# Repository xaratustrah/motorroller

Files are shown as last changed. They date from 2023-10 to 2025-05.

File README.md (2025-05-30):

# motorroller - Open hardware open software stepper motor controller

<div style="margin-left:auto;margin-right:auto;text-align:center">
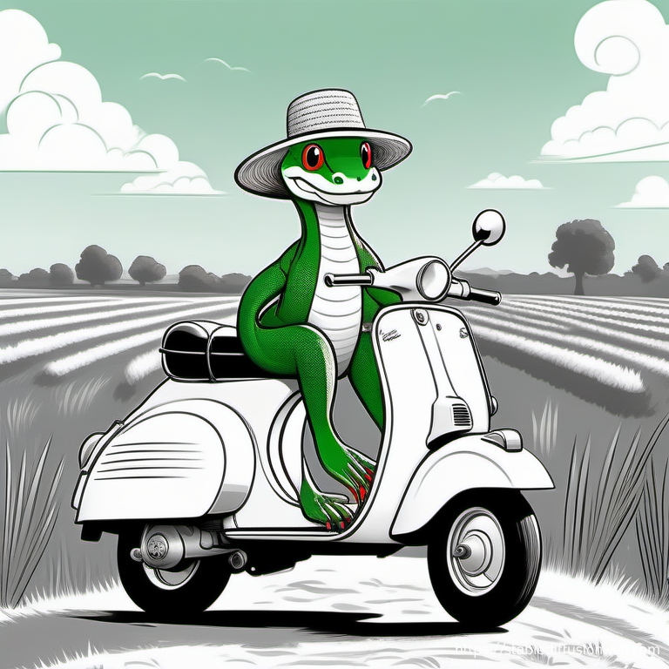
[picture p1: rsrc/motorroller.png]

</div>

`motorroller` is an easy to use open hardware open software stepper motor controller using Raspberry Pi. Depending on which driver you use, you can control 5 phase or 2 phase stepper motors. In this current configuration, it can control up to 4 motors. Also supported are the readout of linear potentiometers.

## Software installation

### Raspberry Pi OS
Please download the latest version of [Raspberry Pi OS Lite](https://www.raspberrypi.com/software/). Newest versions require setting up username / password already in the imager tool. You can also enable SSH from there.

### Raspi-config
Then you can expand file system using the script `raspi-config` and also enable `SPI`.

### Packages
Install some useful packages:

```bash
sudo apt udpate
sudo apt install -y screen mc tree git python3-pip emacs-nox htop sshfs

```

Then install python packages. You may need to provide the command line arg `--break-system-packages`  depending on your system, but be careful with that:

```bash
pip3 install --break-system-packages RPi.GPIO spidev loguru

```

### Repository

Clone and install the repository:

```bash
cd git
git clone https://github.com/xaratustrah/motorroller
cd motorroller
pip3 install --break-system-packages -r requirements.txt
```

The recommended usage is calling the script directly:

```bash
python3 -m motorroller
```

It is also possible to install `motorroller` in the environment, but for this internet connection might be necessary:

```bash
pip3 install --break-system-packages .
```

For uninstalling both you can type:

```bash
pip3 uninstall --break-system-packages motorroller
```

## Usage

### Running modes

`motorroller` can be run in two different modes (the third client/server mode has not been implemented at this stage). It accepts commands in interactive and command line mode. During movement, pressing `ctrl-C` will stop the movement and exit gracefully.

**NOTE:** during any operation, in case of crash due to any reasons, make sure to re-run the code and close down properly, in order to make sure that system is gracefully shut down. This is specially important because of the magnetic break of the motors. The code makes sure that they are gently released after each operation. In case of an unexpected crash it might happen that this gentle close down is not accomplished. So by re-running the code and gently closing again, this will be guaranteed.

#### Interactive mode

this is the default mode. There will be an input prompt for entering commands. Just run:

```bash
python3 -m motorroller
```

The readline history is activated for convenience. You can revisit your older commands by pressing arrow up.

#### Commands as arguments
Use one or several commands directly in the command prompt:

```bash
python3 -m motorroller --command 0i200 0o200
```

Moves motor 0 in and out for 200 steps. Moving motors inside and outside is always in number of steps, but the read out will print out the position values in mm.

### Command structure

Format is XYZ, where X is one of the following:

```
0 --> Motor 0
1 --> Motor 
2 --> Motor 2
3 --> Motor 3

7 --> Both motors 0 and 1
8 --> Both motors 2 and 3

9 --> Read out potentiometers only, the other two positions will be ignored

Y is the direction either I for in or O for out (case insensitive)

Z is the number of steps (int)
```

For example `0i200` means move motor 0 inside 200 steps.

**Special case of command 9:**

Command 9 is just a reader, which means it does not matter what arguments are given, it will always read out the position potentiometers. So in the case of command 9, the only significant value is the number 9 itself, meaning that all other combinations are ignored.

For example the command `9i0` is the same as `9o56879` and so on.

**NOTE:** all commands are case insensitive, i.e. `i`and `I` are equal, same applies to `o`and `O`.

### Other features
Following features work in combination with all above mentioned operation modes:

#### Logger

A logger file name can be provided in order to put actions and readout information together with a time stamp in a log file. You activate the logger by using the `--log` switch:

```bash
python3 -m motorroller --log ./logfile.txt
```

#### Calibration file
Working with a calibration file insures a safer operation. In the calibration file, which is [TOML format](https://toml.io/en/) limits can be set for every motor. You can provide the name of the calibration file as a command line argument:

```bash
python3 -m motorroller --log ./logfile.txt --cal clibration.toml
```

This works for all modes of operation. Here is the structure of the calibration file, with example values:

```toml
# Configuration and calibration file for Motorroller

[general]
minimum_delay = 0.002 # this slows down the movement. recommended value: 0.002

# calibration point format [mm, ADC value]

[mot0]
limit_outside = 30
limit_inside = 70
cal_points = [[90, 869], [10, 3049]]

[mot1]
limit_outside = 30
limit_inside = 70
cal_points = [[90, 857], [10, 3047]]

[mot2]
limit_outside = 30
limit_inside = 70
cal_points = [[90, 831], [10, 3011]]

[mot3]
limit_outside = 30
limit_inside = 70
cal_points = [[90, 877], [10, 3039]]
```

**NOTE:** Calibration point format is [mm, ADC value]. For calibration points, within each pair, please use either floats or integers, TOML format does not allow mixing. As you know the ADC values are always integers, but position values can be floats. If you choose to have a position value that is a float, then you might need to indicate the ADC value also as a float, with ".0" at the end.

For example allowed values: `[90, 831]` or something like `[90.5, 831.0]` but not allowed: `[90.5, 831]`

**NOTE:** Please note that in the current hardware configuration, as motors move inside:

* values in mm increase
* ADC values decrease
* Motor rotation direction would correspond to CCW

## Hardware description

This version of `motorroller` does not use hardware or software PWM, but instead, for increase of accuracy, it uses exact number of steps. This way, you can keep track of the motor motions for more scalability and reproducibility.

#### Board and Schematics

Motorroller

The schematics has been creating using [KiCAD](https://www.kicad.org/). The schematics file is included in the project. A PDF version of the schematics (connection plan) can be found [here](https://github.com/xaratustrah/motorroller/blob/main/rsrc/motorroller.kicad_sch.pdf). Needed parts are listed also in an spread sheet document [here](https://github.com/xaratustrah/motorroller/blob/main/rsrc/motorroller_part_list.ods).

#### Pin configurations

This is the connection table for the 9 pin D-SUB connector:

| Pin # | Signal |
|---|---|
| 1 | End switch outside limit |
| 2 | N. C. |
| 3 | End switch GND |
| 4 | End switch inside limit  |
| 5 | N. C. |
| 6 | Poti GND |
| 7 | Poti runner |
| 8 | Poti PWR |
| 9 | N. C. |

This is the connection table for round motor connector:

| Pin | Signal |
|-----|---|
| A | Blue |
| B | Green |
| C | Red |
| D | Black |
| E | Orange |
| F | N. C. |
| G | N. C. |
| H | N. C. |
| J | N. C. |
| K | N. C. |
| L | Break PWR |
| M | Break GND |

#### Additional hints

* Please note that the driver has direct opto-coupler inputs, whereas the relay board has opto-couplers that are already pulled up to 5V on one side.

* For crimping the wires, please note that for the crimp tool you need to set level 8 for 0.75mm<sup>2</sup> which are the motor cables, and level 5 for 0.14mm<sup>2</sup> cables, which are the end switch and potentiometer cables.

#### End switches

Although end switches are connected in the hardware, please be aware that in the current version the end switches are *NOT* implemented. There is however a "soft" end switch that is implemented, whose ranges are set in the TOML file.

For example: while the full range of motor movements is 0mm to 100 mm, it is possible to set the limits to 30mm to 70mm.

The software based end switch will not allow any further movement when the motor has entered the limit zone. But it still allows moving past the limit when motor enters from an allowed zone.

For example: if the limit is set to 70mm, and the motor is currently at 65mm, then moving the motors by 10mm will move them past the 70mm limit to 75mm. Issuing any further command in that direction will be caught by the software end switch.

For this reason it is important to always move the motors in a series of SMALL movements and always keep an eye on the current position readout on the display.

*IMPORTANT*: please always move motors in smaller number of steps:

For example moving motor 0 inwards for 1000 steps: 0i1000

#### Outlook / future revisions

Here are some suggestions for an upgrade. In case a PCB is created for the project, it is recommended that the following be considered:

* Use SPI based IO-expander **MCP23S08** in order to read the status of the end switches. This one would share the same SCLK, MOSI and MISO lines with the MCP2308 but would need its own chip select signal. This would be then connected to **pin 26** of the Raspberry Pi header.

A hardware platform has been recently developed that can be used for future versions of `motorroller` and can be found [on this repository](https://github.com/DouniaBoudefla/piadcio). Please also have a look at another similar project called [daedalus](https://github.com/xaratustrah/daedalus/).

In order to have the analog signals of the potentiometers and the digital signals of the end switches, one should use the 10-pin header, and connect via flat cable to 9-pin D-SUB connector to the front plate. **Please notice, that the 10-pin connector has a different counting direction if connected to flat-cable D-SUB connectors!**

* Change relay order

For the next revision, the relay order for the BRK signals could be made more symmetric around the relay board connector:

| Pin # | Rev 0 | Rev 0 connection | Future connection |
|---|---|---|---|
| 1 | 5V | 5V | 5V |
| 2 | 5V | 5V | 5V |
| 3 | REL1  | motor_select | motor_select |
| 4 | REL2  | motor_select | motor_select |
| 5 | REL3  | motor_select | motor_select |
| 6 | REL4  | motor_select | motor_select |
| 7 | REL5  | motor_select | motor_select |
| 8 | REL6  | brk0 | brk0 |
| 9 | REL7  | driver_select | brk1 |
| 10 | REL8  | driver_select | driver_select |
| 11 | REL9  | brk1 | driver_select |
| 12 | REL10 | brk2 | brk3 |
| 13 | REL11 | brk3 | brk2 |
| 14 | REL12 | motor_select | motor_select |
| 15 | REL13 | motor_select | motor_select |
| 16 | REL14 | motor_select | motor_select |
| 17 | REL15 | motor_select | motor_select |
| 18 | REL16 | motor_select | motor_select |
| 19 | GND | GND | GND |
| 20 | GND | GND | GND |

* Level shifters
  
This is a nice to have option, just add two level shifters for the CCW and CLW signals. In principle, a level shifter can also replace the darlington array IC ULN2003A , which is a bit of an overkill for the current purpose.

## Licensing

Please see the file [LICENSE.md](./LICENSE.md) for further information about how the content is licensed.

## Acknowledgements

Many thanks to Robert Boywitt, Roland Fischer and Sven Schuhmacher for helping with the connection plans and correct identification of the parts, and Davide Racano for providing help with the mechanical preparation of the enclosure.

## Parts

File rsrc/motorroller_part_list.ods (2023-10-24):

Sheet: Part Numbers
Part list for Motorroller
https://github.com/xaratustrah/motorroller
How many | Part | Brand | Distributor | Distro Order # | Description
2 | - | - | Conrad | 189626 | IC-Fassung Rastermaß: 7.62 mm, 2.54 mm Polzahl (num): 16 Präzisions-Kontakte
1 | AWHW 20G-0202-T | Assmann | RS | 113-5959 | ASSMANN WSW AWHW Leiterplatten-Stiftleiste Stecker Abgewinkelt, 20-polig / 2-reihig, Raster 2.54mm,
4 | AWHW 10G-0202-T | Assmann | RS | 674-1230 | ASSMANN WSW AWHW Leiterplatten-Stiftleiste Stecker Gerade, 10-polig / 2-reihig, Raster 2.54mm, Lötanschluss-Anschluss,
1 | AWHW 40G-0202-T | Assmann | RS | 674-1252 | ASSMANN WSW AWHW Leiterplatten-Stiftleiste Stecker Gerade, 40-polig / 2-reihig, Raster 2.54mm, Lötanschluss-Anschluss
 | AWP 10-7240-T | Assmann | RS | 674-1097 | ASSMANN WSW AWP IDC-Steckverbinder Buchse, gewinkelt, 10-polig / 2-reihig, Raster 2.54mm
2 | AWP 20-7240-T | Assmann | RS | 674-1104 | ASSMANN WSW AWP IDC-Steckverbinder Buchse, gewinkelt, 20-polig / 2-reihig, Raster 2.54mm
2 | AWP 40-7240-T | Assmann | RS | 674-1110 | ASSMANN WSW AWP IDC-Steckverbinder Buchse, gewinkelt, 40-polig / 2-reihig, Raster 2.54mm
4 | DS1033-09FBNSISS-CT | Connfly | Conrad | 1389963 | D-SUB Buchse 180 ° Polzahl (num): 9 Löten
2 | GTR515B | GMT Global | optik-mechanik.de | GTR515B | 5 Phase motor level converter / driver
1 | MCP3208 | Microchip | Conrad | 651465 | Analog to digital converter
1 | Raspberry Pi 3B+ | Raspberry Pi 3B+ | - | - | Raspberry Pi 3B+
1 | - | RS Pro | RS | 188-1318 | RS PRO 19 Zoll Rack Gehäuse 2U Schwarz, 425 mm x 425mm x 84 mm
1 |  | RS Pro | RS | 361-658 | RS PRO Einzeladerleitung 0,75 mm², 18 AWG 100m Blau PVC isoliert Ø 2.7mm 24 / 0,2 mm Litzen
1 |  | RS Pro | RS | 361-709 | RS PRO Einzeladerleitung 0,75 mm², 18 AWG 100m Gelb PVC isoliert Ø 2.7mm 24 / 0,2 mm Litzen
1 |  | RS Pro | RS | 836-0782 | RS PRO Einzeladerleitung 0,75 mm², 18 AWG 100m Grau PVC isoliert Ø 2.7mm 24 / 0,2 mm Litzen
1 |  | RS Pro | RS | 196-4313 | RS PRO Einzeladerleitung 0,75 mm², 18 AWG 100m Grün PVC isoliert Ø 2.7mm 24 / 0,2 mm Litzen
1 |  | RS Pro | RS | 196-4317 | RS PRO Einzeladerleitung 0,75 mm², 18 AWG 100m Rosa PVC isoliert Ø 2.7mm 24 / 0,2 mm Litzen
1 |  | RS Pro | RS | 361-686 | RS PRO Einzeladerleitung 0,75 mm², 18 AWG 100m Rot PVC isoliert Ø 2.7mm 24 / 0,2 mm Litzen
1 |  | RS Pro | RS | 361-642 | RS PRO Einzeladerleitung 0,75 mm², 18 AWG 100m Schwarz PVC isoliert Ø 2.7mm 24 / 0,2 mm Litzen
1 | - | RS Pro | RS | 289-9846 | RS PRO Flachbandkabel , 10-adrig, Raster 1.27mm Nicht abgeschlossen 12,7 mm
1 | - | RS Pro | RS | 289-9896 | RS PRO Flachbandkabel , 20-adrig, Raster 1.27mm Nicht abgeschlossen 25,4 mm
1 | - | RS Pro | RS | 289-9975 | RS PRO Flachbandkabel , 40-adrig, Raster 1.27mm Nicht abgeschlossen 50,8 mm
4 | - | RS Pro | RS | 494-8912 | RS PRO Printklemme / Stecker , THT, 3-polig / 1-reihig, Raster 5mm
2 | - | RS Pro | RS | 897-1332 | RS PRO Printklemme / Stecker, THT, 2-polig / 1-reihig, Raster 3.5mm
4 | - | RS Pro | RS | 137-957 | RS PRO Sub-D Steckverbinder Buchse, 9-polig / Raster 1.27mm, Kabelmontage IDC
1 | 4301.1407 | Schurter | Distrelec | 169-62-956 | Fuse drawer for DD11.0114.1111
1 | DD11.0114.1111 | Schurter | Distrelec | 169-63-555 | Inlet, C14, 250V, Schurter, 1-pole fuse holder, illuminated green
1 | RC320-07 | Schurter | Distrelec | 303-02-323 | Rear cover, protection
5 | SMQ1089 | Signal Construct | Conrad | 185949 | Signal Construct SMQ1089 SMQ1089 LED-Fassung Metall Passend für (LEDs) LED 5 mm Schraubbefestigung
4 | UTG01412SH | SOURIAU-SUNBANK / EATON | Farnell | 2249934 | 12 pol round connector wall mount female
48 | RC16M23K | SOURIAU-SUNBANK / EATON | Farnell | 3652051 | Cup pins for UTG01412SH
1 | ULN2003A | ST | Conrad | 177970 | Darlington array
1 | TPP-65-3512 | Traco Power | Conrad | 1591563 | TracoPower TPP 65-3512 AC/DC-Netzteilbaustein, open frame 24 V/DC 2.71 A
1 | TC-9445344 | TRU Components | Conrad | 2361336 | Relayboard with 16 relays
1 | 1408770 | TRU Components | Conrad | 1408770 | TRU COMPONENTS RJ45-01 RJ45-Einbaubuchse 1408770 Buchse, Einbau, Stecker, gerade Polzahl 8P8C Silber
4 | TC-02747-10-1-00-2 | TRU Components | Conrad | 1560763 | TRU COMPONENTS TC-02747-10-1-00-2 Stiftleiste Rastermaß: 2.54 mm Polzahl Gesamt: 10 Anzahl Reihen: 2
1 | TC-02747-20-1-00-2 | TRU Components | Conrad | 1560662 | TRU COMPONENTS TC-02747-20-1-00-2 Stiftleiste Rastermaß: 2.54 mm Polzahl Gesamt: 20 Anzahl Reihen: 2
1 | TC-02747-40-1-00-2 | TRU Components | Conrad | 1560769 | TRU COMPONENTS TC-02747-40-1-00-2 Stiftleiste Rastermaß: 2.54 mm Polzahl Gesamt: 40 Anzahl Reihen: 2
1 | 1229322 | TRU Components | Conrad | 1229322 | USB-Doppeleinbaubuchse 2.0 Buchse, Einbau USB-06-BK 2 x USB-Buchse Typ A auf 2 x USB-Stecker Typ A mit 60 cm Kabel 12293
1 | L-53 LGD | Kingbright | Conrad | 146030 | Kingbright L 53 LGD LED bedrahtet Grün Rund 5 mm 2 mcd 60 ° 2 mA 2.2 V
1 | L-53 LID | Kingbright | Conrad | 146005 | Kingbright L 53 LID LED bedrahtet Rot Rund 5 mm 5 mcd 60 ° 2 mA 2 V
1 | TC-8990608 | TRU Components | Conrad | 2247652 | TRU COMPONENTS Strom-Kabel Raspberry Pi [1x USB 2.0 Stecker Micro-B - 1x offene Kabelenden] 1.00 m Schwarz
 |  |  |  |  | Schrauben für SUB-D
1 | MH860 | GLENAIR | Farnell | 105992 | GLENAIR MH860 Crimpwerkzeug, Crimpzange, 22-16AWG Contacts
1 | MH86-164G | DANIELS | Farnell | 151779 | Positionierer für Crimpwerkzeuge, Steckverbinder Fci Trim Trio Metalok Bantam Qikmate
1 | RX2025GE1 | SOURIAU-SUNBANK / EATON | Farnell | 105498 | Ausziehwerkzeug, Kontakten der Baureihe TRIM TRIO von Souriau, #16, Souriau Trim Trio

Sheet: Relay Board Connector
Name | Pin # | Function
5V | 1 | PWR
5V | 2 | PWR
REL1 | 3 | BLUE
REL2 | 4 | BLUE
REL3 | 5 | BLUE
REL4 | 6 | BLUE
REL5 | 7 | BLUE
REL6 | 8 | BRK0
REL7 | 9 | DRV-SEL
REL8 | 10 | DRV-SEL
REL9 | 11 | BRK1
REL10 | 12 | BRK2
REL11 | 13 | BRK3
REL12 | 14 | GREEN
REL13 | 15 | GREEN
REL14 | 16 | GREEN
REL15 | 17 | GREEN
REL16 | 18 | GREEN
GND | 19 | PWR
GND | 20 | PWR

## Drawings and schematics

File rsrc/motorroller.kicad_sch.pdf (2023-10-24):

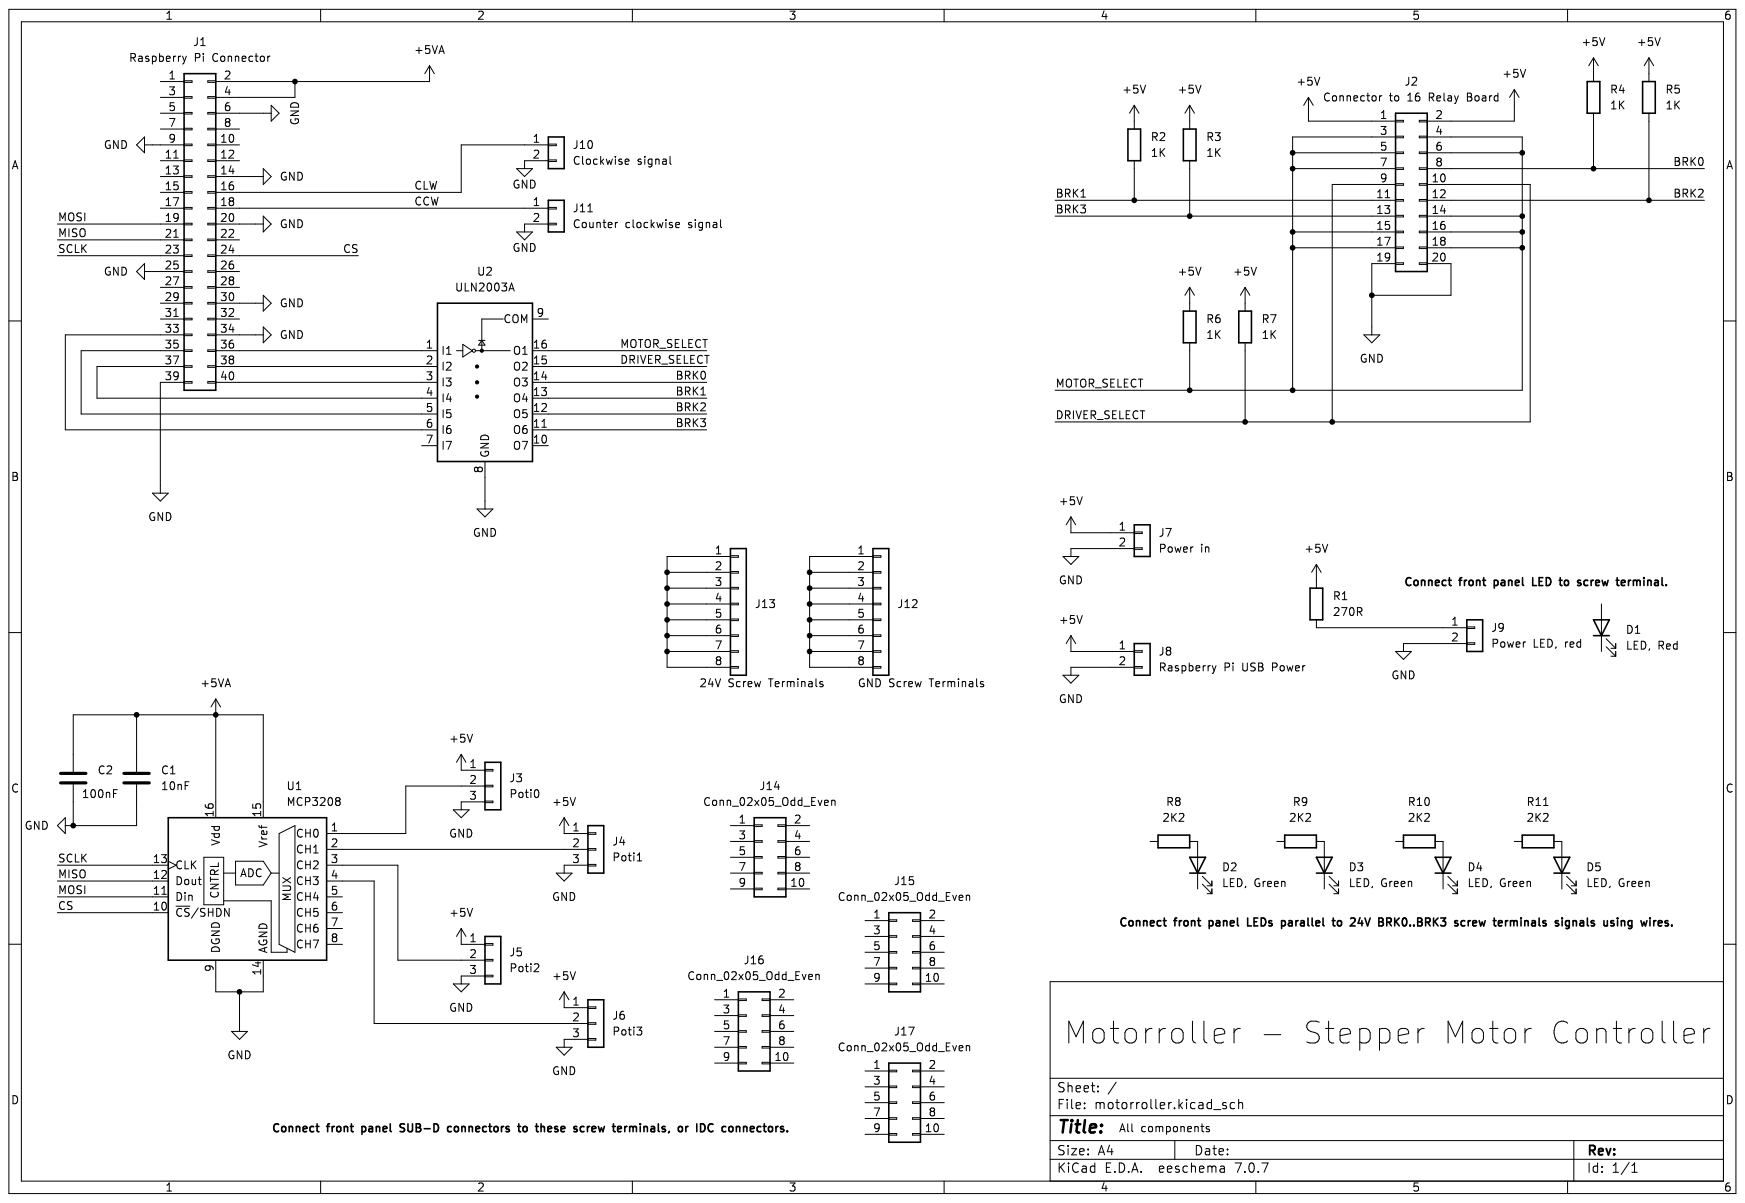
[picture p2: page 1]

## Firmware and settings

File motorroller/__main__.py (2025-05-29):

"""
Motorroller - Open hardware open software stepper motor controller

2023 xaratustrah@github
"""

from time import sleep
import argparse
import os
import sys
from loguru import logger
import toml
from .version import __version__

if os.name == "posix" and os.uname().machine == "armv7l":
    try:
        import RPi.GPIO as gpio
        import spidev
    except RuntimeError:
        print("""Error importing Raspberry Pi libraries!""")
else:
    print("Are you running the code on a Raspberry Pi?")
    exit()

# Raspberry PI pin assignment

CLW = 16
CCW = 18

BRK0 = 40
BRK2 = 35
BRK1 = 37
BRK3 = 33

MOTOR_SELECT = 36
DRIVER_SELECT = 38

class Motorroller:
    def __init__(self, calibration_dic):
        self.brk_list = [BRK0, BRK1, BRK2, BRK3]
        self.spi_init()
        self.gpio_setup()
        self.gpio_reset()
        self.calibration_dic = calibration_dic

    def gpio_setup(self):
        # gpio Setup
        gpio.setwarnings(False)
        gpio.setmode(gpio.BOARD)  # Header pin number system

        gpio.setup(CLW, gpio.OUT)
        gpio.setup(CCW, gpio.OUT)
        gpio.setup(BRK0, gpio.OUT)
        gpio.setup(BRK1, gpio.OUT)
        gpio.setup(BRK2, gpio.OUT)
        gpio.setup(BRK3, gpio.OUT)
        gpio.setup(MOTOR_SELECT, gpio.OUT)
        gpio.setup(DRIVER_SELECT, gpio.OUT)

    def spi_init(self):
        # init SPI
        self.spi = spidev.SpiDev()
        self.spi.open(0, 0)
        self.spi.max_speed_hz = 5000
        return self.spi

    def gpio_reset(self):
        # Initial values
        gpio.output(CLW, gpio.LOW)
        gpio.output(CCW, gpio.LOW)

        gpio.output(MOTOR_SELECT, gpio.LOW)
        gpio.output(DRIVER_SELECT, gpio.LOW)

        for channel in {0, 1, 2, 3}:
            gpio.output(self.brk_list[channel], gpio.LOW)

    @staticmethod
    def get_mm_from_adcval(adc_val, p1, p2):
        x1, y1 = p1[0], p1[1]
        x2, y2 = p2[0], p2[1]
        return (x2 - x1) / (y2 - y1) * (adc_val - y1) + x1

    @staticmethod
    def get_adcval_from_mm(mm, p1, p2):
        x1, y1 = p1[0], p1[1]
        x2, y2 = p2[0], p2[1]
        return (y2 - y1) / (x2 - x1) * (mm - x1) + y1

    def read_poti(self, channel):
        msg = (
            0x00
            if channel == 0
            else 0x40
            if channel == 1
            else 0x80
            if channel == 2
            else 0xC0
        )

        resp = self.spi.xfer([0x06, msg, 0x00])
        value = (resp[1] << 8) + resp[2]
        value = int(value)

        # clip value
        if value <= 0:
            value = 0
        elif value > 4095:
            value = 4095

        return value

    def read_all_potis(self):
        sleep(0.2)
        num_avg = 20
        pot0, pot1, pot2, pot3 = 0, 0, 0, 0
        # do many measurements and average
        for i in range(num_avg):
            pot0 += self.read_poti(0)
            pot1 += self.read_poti(1)
            pot2 += self.read_poti(2)
            pot3 += self.read_poti(3)
        return [
            int(pot0 / num_avg),
            int(pot1 / num_avg),
            int(pot2 / num_avg),
            int(pot3 / num_avg),
        ]

    def move_motor(self, channel, direction, nsteps):
        # first read the potis
        pot0, pot1, pot2, pot3 = self.read_all_potis()

        if channel == 0:
            # first set the flags
            driver_select, motor_select = 0, 0

            # then check limits according to config file
            if self.calibration_dic:
                logger.info(
                    "Checking position values with the limits provided in the calibration file before moving."
                )
                limit_inside = self.calibration_dic["mot0"]["limit_inside"]
                limit_outside = self.calibration_dic["mot0"]["limit_outside"]
                p1 = self.calibration_dic["mot0"]["cal_points"][0]
                p2 = self.calibration_dic["mot0"]["cal_points"][1]
                logger.info(
                    f"Using calibration points: {p1, p2}, direction {direction}, inside limit {limit_inside} and outside limit {limit_outside}"
                )

                if (
                    pot0 <= self.get_adcval_from_mm(limit_inside, p1, p2)
                    and direction == "ccw"
                ):
                    logger.error(
                        "Motor mot0 limit_inside position reached. Cannot move any further in that direction."
                    )
                    return
                elif (
                    pot0 >= self.get_adcval_from_mm(limit_outside, p1, p2)
                    and direction == "clw"
                ):
                    logger.error(
                        "Motor mot0 limit_outside position reached. Cannot move any further in that direction."
                    )
                    return
                else:
                    logger.info(
                        "Motor mot0 still in the given range of calibration file. Moving..."
                    )

        if channel == 1:
            # first set the flags
            driver_select, motor_select = 0, 1

            # then check limits according to config file
            if self.calibration_dic:
                logger.info(
                    "Checking position values with the limits provided in the calibration file before moving."
                )
                limit_inside = self.calibration_dic["mot1"]["limit_inside"]
                limit_outside = self.calibration_dic["mot1"]["limit_outside"]
                p1 = self.calibration_dic["mot1"]["cal_points"][0]
                p2 = self.calibration_dic["mot1"]["cal_points"][1]
                logger.info(
                    f"Using calibration points: {p1, p2}, direction {direction}, inside limit {limit_inside} and outside limit {limit_outside}"
                )

                if (
                    pot1 <= self.get_adcval_from_mm(limit_inside, p1, p2)
                    and direction == "ccw"
                ):
                    logger.error(
                        "Motor mot1 limit_inside position reached. Cannot move any further in that direction."
                    )
                    return
                elif (
                    pot1 >= self.get_adcval_from_mm(limit_outside, p1, p2)
                    and direction == "clw"
                ):
                    logger.error(
                        "Motor mot1 limit_outside position reached. Cannot move any further in that direction."
                    )
                    return
                else:
                    logger.info(
                        "Motor mot1 still in the given range of calibration file. Moving..."
                    )

        if channel == 2:
            # first set the flags
            driver_select, motor_select = 1, 0

            # then check limits according to config file
            if self.calibration_dic:
                logger.info(
                    "Checking position values with the limits provided in the calibration file before moving."
                )
                limit_inside = self.calibration_dic["mot2"]["limit_inside"]
                limit_outside = self.calibration_dic["mot2"]["limit_outside"]
                p1 = self.calibration_dic["mot2"]["cal_points"][0]
                p2 = self.calibration_dic["mot2"]["cal_points"][1]
                logger.info(
                    f"Using calibration points: {p1, p2}, direction {direction}, inside limit {limit_inside} and outside limit {limit_outside}"
                )

                if (
                    pot2 <= self.get_adcval_from_mm(limit_inside, p1, p2)
                    and direction == "ccw"
                ):
                    logger.error(
                        "Motor mot2 limit_inside position reached. Cannot move any further in that direction."
                    )
                    return
                elif (
                    pot2 >= self.get_adcval_from_mm(limit_outside, p1, p2)
                    and direction == "clw"
                ):
                    logger.error(
                        "Motor mot2 limit_outside position reached. Cannot move any further in that direction."
                    )
                    return
                else:
                    logger.info(
                        "Motor mot2 still in the given range of calibration file. Moving..."
                    )

        if channel == 3:
            # first set the flags
            driver_select, motor_select = 1, 1

            # then check limits according to config file
            if self.calibration_dic:
                logger.info(
                    "Checking position values with the limits provided in the calibration file before moving."
                )
                limit_inside = self.calibration_dic["mot3"]["limit_inside"]
                limit_outside = self.calibration_dic["mot3"]["limit_outside"]
                p1 = self.calibration_dic["mot3"]["cal_points"][0]
                p2 = self.calibration_dic["mot3"]["cal_points"][1]
                logger.info(
                    f"Using calibration points: {p1, p2}, direction {direction}, inside limit {limit_inside} and outside limit {limit_outside}"
                )

                if (
                    pot3 <= self.get_adcval_from_mm(limit_inside, p1, p2)
                    and direction == "ccw"
                ):
                    logger.error(
                        "Motor mot3 limit_inside position reached. Cannot move any further in that direction."
                    )
                    return
                elif (
                    pot3 >= self.get_adcval_from_mm(limit_outside, p1, p2)
                    and direction == "clw"
                ):
                    logger.error(
                        "Motor mot3 limit_outside position reached. Cannot move any further in that direction."
                    )
                    return
                else:
                    logger.info(
                        "Motor mot3 still in the given range of calibration file. Moving..."
                    )

        # now you can start moving the motors
        gpio.output(DRIVER_SELECT, driver_select)
        gpio.output(MOTOR_SELECT, motor_select)
        
        # disengaging the breaks
        gpio.output(self.brk_list[channel], 1)

        if direction == "ccw":
            
            for i in range(nsteps):
                ramp = 0.02/((i+1)*10)
                if ramp < self.calibration_dic["general"]["minimum_delay"]:
                    ramp = self.calibration_dic["general"]["minimum_delay"]
                gpio.output(CCW, gpio.HIGH)
                sleep(ramp)
                gpio.output(CCW, gpio.LOW)
                sleep(ramp)
        else:
            for i in range(nsteps):
                ramp = 0.02/((i+1)*10)
                if ramp < self.calibration_dic["general"]["minimum_delay"]:
                    ramp = self.calibration_dic["general"]["minimum_delay"]
                gpio.output(CLW, gpio.HIGH)
                sleep(ramp)
                gpio.output(CLW, gpio.LOW)
                sleep(ramp)

        # engaging the breaks again
        gpio.output(self.brk_list[channel], 0)

    def closedown(self):
        self.spi.close()
        self.gpio_reset()

    def process_command(self, cmd):
        valid_channels = {0, 1, 2, 3, 7, 8, 9}
        valid_directions = {"i", "I", "o", "O"}

        try:
            assert len(cmd) >= 3

            first_char = int(cmd[0])
            second_char = cmd[1]

            assert first_char in valid_channels
            assert second_char in valid_directions

        except (AssertionError, ValueError):
            raise ValueError(
                """Command format incorrect. Please use the following format:

                    Format is XYZ, where X is one of the following:

                    0 --> Motor 0
                    1 --> Motor 1
                    2 --> Motor 2
                    3 --> Motor 3

                    7 --> Both motors 0 and 1
                    8 --> Both motors 2 and 3

                    9 --> Read out potentiometers only, the other two positions will be ignored

                    Y is the direction either I for in or O for out (case insensitive)

                    Z is the number of steps (int) \n
                """
            )

        channel = int(first_char)

        # assign CCW to the direction of in
        direction = "ccw" if second_char in {"i", "I"} else "clw"

        # Try to cast number of steps to an integer
        if len(cmd) == 3:
            s = cmd[2]
        else:
            s = cmd[2:]

        try:
            nsteps = int(s)  # Try to cast as an integer
        except ValueError:
            raise ValueError("Could not extract an integer from the command string.")

        return channel, direction, nsteps

    def log_poti_values(self):
        pot_vals = self.read_all_potis()
        poti_string = (
            f"Poti values: {self.read_all_potis()}"
            if not self.calibration_dic
            else f"""Poti values: {pot_vals}, Positions in mm: {self.get_mm_from_adcval(pot_vals[0], self.calibration_dic["mot0"]["cal_points"][0], self.calibration_dic["mot0"]["cal_points"][1]):.2f}, {self.get_mm_from_adcval(pot_vals[1], self.calibration_dic["mot1"]["cal_points"][0], self.calibration_dic["mot1"]["cal_points"][1]):.2f}, {self.get_mm_from_adcval(pot_vals[2], self.calibration_dic["mot2"]["cal_points"][0], self.calibration_dic["mot2"]["cal_points"][1]):.2f}, {self.get_mm_from_adcval(pot_vals[3], self.calibration_dic["mot3"]["cal_points"][0], self.calibration_dic["mot3"]["cal_points"][1]):.2f}"""
        )
        logger.info(poti_string)

    def process_action(self, command_str):
        channel, direction, nsteps = self.process_command(command_str)
        if channel in {0, 1, 2, 3}:
            logger.info(
                f"Moving motor {channel}, direction {direction} for {nsteps} steps."
            )
            self.move_motor(channel, direction, nsteps)
            self.log_poti_values()
        elif channel == 7:
            logger.info(
                f"Moving motors 0 and 1, direction {direction} for {nsteps} steps."
            )
            self.move_motor(0, direction, nsteps)
            self.move_motor(1, direction, nsteps)
            self.log_poti_values()
        elif channel == 8:
            logger.info(
                f"Moving motors 2 and 3, direction {direction} for {nsteps} steps."
            )
            self.move_motor(2, direction, nsteps)
            self.move_motor(3, direction, nsteps)
            self.log_poti_values()
        elif channel == 9:
            self.log_poti_values()


# -------


def start_interactive_mode(motorroller):
    while True:
        try:
            command_str = input("Enter command or ctrl-C or ctrl-D to abort-->")
            motorroller.process_action(command_str)

        except (EOFError, KeyboardInterrupt):
            logger.success("\nUser input cancelled. Aborting...")
            break

        except ValueError as e:
            print(e)


def start_single_mode(motorroller, command_str_list):
    try:
        for command in command_str_list:
            motorroller.process_action(command)

    except (EOFError, KeyboardInterrupt):
        logger.success("\nUser input cancelled. Aborting...")

    except ValueError as e:
        print(e)



def start_server_mode():
    logger.error("Client / Server mode not implemented yet.")


def validate_config(config):
    required_keys = [
        "general.minimum_delay",
        "mot0.limit_outside",
        "mot0.limit_inside",
        "mot0.cal_points",
        "mot1.limit_outside",
        "mot1.limit_inside",
        "mot1.cal_points",
        "mot2.limit_outside",
        "mot2.limit_inside",
        "mot2.cal_points",
        "mot3.limit_outside",
        "mot3.limit_inside",
        "mot3.cal_points",
    ]
    for key in required_keys:
        keys = key.split(".")
        conf = config
        for k in keys:
            if k not in conf:
                raise ValueError(f"Missing required key: {key}")
            conf = conf[k]

# -------


def main():
    parser = argparse.ArgumentParser(prog="motorroller")
    parser.add_argument(
        "-c",
        "--command",
        nargs="+",
        type=str,
        help="Enter command as an argument.",
        default=None,
    )
    parser.add_argument(
        "--server",
        action=argparse.BooleanOptionalAction,
        help="Start in client / server mode.",
    )
    parser.add_argument(
        "-v", "--version", action="version", version=__version__, help="Print version."
    )
    parser.add_argument(
        "-l", "--log", nargs=1, type=str, help="Path and name of the log file."
    )

    parser.add_argument(
        "--cal",
        nargs=1,
        type=str,
        default=None,
        help="Path and name of the calibration file.",
    )

    logger.remove(0)
    logger.add(sys.stdout, level="INFO")
    # logger.patch(lambda record: record.update(name=record["file"].name))

    args = parser.parse_args()

    # read config file
    cal_dic = None
    if args.cal:
        logger.info("Calibration file has been provided.")
        try:
            # Load calibration file
            cal_dic = toml.load(args.cal[0])
            validate_config(cal_dic)
        except:
            logger.error('Calibration file does not have required format.')
            exit()
        logger.success("Calibration file is good.")
    else:
        logger.warning(
            "No calibration file provided. Aborting..."
        )
        exit()

    # ready to go
    motorroller = Motorroller(cal_dic)

    if args.log:
        outfilename = args.log[0]
        # all levels
        logger.add(f"{outfilename}.log")

    if args.command:
        logger.info("Running individual commands.")
        start_single_mode(motorroller, args.command)

    elif args.server:
        logger.info("Starting client / server mode.")
        start_server_mode(motorroller)

    else:
        logger.info("Starting interactive mode.")
        start_interactive_mode(motorroller)

    # gracefully close down
    motorroller.closedown()
    exit()


# -----
if __name__ == "__main__":
    main()

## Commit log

2023-10-24 bump version
    [motorroller.kicad_sch]
2023-10-24 add command processor
    [motorroller_part_list.ods]
2023-10-24 did a lot
    [motorroller.kicad_sch, pin_connections.ods]
2023-10-25 new driver
    [pin_connections.ods]
2025-05-29 do not work if no cal file provided
    [__main__.py]
